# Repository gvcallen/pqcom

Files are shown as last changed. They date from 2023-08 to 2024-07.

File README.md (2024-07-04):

# PocketQube Satellite Communication System

## Overview
This repository holds code, datasheets, PCB schematics and other files related to the design and development of a PocketQube Satellite Communication System. This was done by Gary Allen in  partial fulfilment of the requirements of the module Project (E) 448 for the degree Baccalaureus in Engineering in the Department of Electrical and Electronic Engineering at the University of Stellenbosch, South Africa. PocketQubes are miniaturised satellites, and this project aimed to develop prototypes for the unit to be placed on the satellite, the ground station, and the PC interface. A video documenting the project can be found on YouTube at https://www.youtube.com/watch?v=bJcF6t-W-kM

## Code
This folder contains the relevant code for the project. Inside are 5 sub-folders. All embedded development was done using the *PlatformIO* extension on VS code, and all desktop GUI development was done using the *Qt* C++ library, both under WSL (Windows Subsystem for Linux). I highly recommend a linux install due to the ease of installation of the Qt libraries.
- ***gel*** is another Github repository created by myself containing the core embedded C++ classes used by the other projects. Even though it was developed solely for this project, I decided to make it an independent library so that it can be self-standing and potentially be used outside of the PocketQube project in the future.
- ***pqcu*** is the folder housing the code for the *PocketQube Communication Unit* i.e. the module to be placed on the PQ itself. It is very simple since it only "spits out" its GPS location via LoRa (i.e only downlink communication was implemented) however "gel" theoretically has an almost-ready foundation for dual-link communication (which was not implemented due to time constraints).
- ***pqgs*** contains code for the *PocketQube Ground Station*. This includes communication with the PQ unit, motor drive control, GPS tracking and serial control via a "TNC" (a.k.a a laptop connected via USB).
- ***pqui*** contains desktop GUI code to control the GS via USB and a PC. Theoretically, all control can be done via the terminal, however the GUI was implemented to make things slightly easier. It implements the SUNCQ protocol under ***Documents***.
- ***radiosonde_auto_rx*** was an extension of the project to receive data from a commercial Radiosonde via a software-defined radio (SDR). This is used by ***pqui***. Although the Radiosonde receiving is functional, it is currently implemented is a bit "messy", since a Python script is called and controlled from Qt, and this causes issues from time-to-time. If only "custom" communication is needed, this can be ignored.

## Other
The rest of the contents are relatively self-explanatory:
- ***datasheets*** contains various used (and not used) datasheets for ICs and modules.
- ***documents*** contains the SUNCQ protocol for PC to GS communication.
- ***images*** contains images taken throughout the project, such as during testing and final deployment.
- ***kicad*** contains the schematics developed for the PQ and the GS. The final Gerber files are also present in zip format. Note that some folders in here are old and need to be cleaned up.
- ***link-budget*** contains a pre-liminary link-budget done with free Python software.
- ***report*** contains the final report files for Latex. The final PDF is in the root of this folder.
- ***testing*** contains test results and data.

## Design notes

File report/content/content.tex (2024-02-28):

\titlespacing*{\chapter}{0pt}{0pt}{20pt}
\chapter{Introduction}
\subfile{introduction/overview}
\subfile{introduction/problem_statement}
\subfile{introduction/requirements}
\subfile{introduction/specifications}

\chapter{Background}
\subfile{background/pocketqube}
\subfile{background/satellite_tracking}
\subfile{background/antennas}
\subfile{background/telecommunication}
% \subfile{background/pcb_design}

\chapter{System Design}
% \subfile{system_design/overview}
\subfile{system_design/high_level_system}
\subfile{system_design/ground_station}
\subfile{system_design/pq_unit}

\chapter{Detailed Design}
\subfile{detailed_design/component_selection}
\subfile{detailed_design/ground_station_pcb}
\subfile{detailed_design/pq_unit_pcb}
\subfile{detailed_design/link_budget}
\subfile{detailed_design/ground_station_antenna}
\subfile{detailed_design/pq_unit_antenna}
\subfile{detailed_design/software}

\chapter{Implementation}
\subfile{implementation/ground_station_pcb}
\subfile{implementation/ground_station_antenna}
\subfile{implementation/pq_unit_pcb}
\subfile{implementation/pq_unit_antenna}
\subfile{implementation/software}

\chapter{Testing}
\subfile{testing/ground_station_pcb}
\subfile{testing/pq_unit_pcb}
\subfile{testing/radio_communication}
\subfile{testing/ground_station_antenna}
\subfile{testing/pq_unit_antenna}
\subfile{testing/gui}
\subfile{testing/range}
\subfile{testing/tracking}
\subfile{testing/radiosonde}
\subfile{testing/full_system}

\chapter{Conclusion}
\subfile{conclusion/summary}
\subfile{conclusion/future_work}

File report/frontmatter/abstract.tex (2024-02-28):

\chapter*{Abstract}
\addcontentsline{toc}{chapter}{Abstract}
\makeatletter\@mkboth{}{Abstract}\makeatother

This report documents the design and implementation of a wireless communication system for a miniaturised satellite called a \textit{PocketQube}. The PocketQube standard is a set of specifications which aim to make it easier for people to design small satellite modules that can easily integrate with each other. The standard is relatively new, however, and few designs have been published for a full PocketQube communication system that includes a ground station.

The design in this project includes both a tracking ground station, as well as a PocketQube module. The LoRa-based ground station was designed to mechanically track the satellite system using a pre-defined GPS path, as well as using satellite-received GPS data. The ground station was also designed to receive telemetry from existing radiosondes in the meteorological band. The system was then implemented, and the LoRa communication link was successfully tested up to 122 km line-of-sight at a baud rate of 9600 bps. This report documents the design choices made and constraints faced; discusses the methods uses during implementation; interprets the test results; and suggests improvements for future projects.

\selectlanguage{english}

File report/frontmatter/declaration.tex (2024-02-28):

%\chapter*{Declaration}
\newpage
\thispagestyle{plain}
\addcontentsline{toc}{chapter}{Declaration}
\makeatletter\@mkboth{}{Declaration}\makeatother

\centerline{}
\vspace*{-10pt}

\section*{\centering Plagiaatverklaring / \textit{Plagiarism Declaration}}

\vspace*{5pt}

\begin{enumerate}
    \item Plagiaat is die oorneem en gebruik van die idees, materiaal en ander intellektuele eiendom van ander persone asof dit jou eie werk is.\\
    \textit{Plagiarism is the use of ideas, material and other intellectual property of another's work
        and to present it as my own.}
    
    \item Ek erken dat die pleeg van plagiaat 'n strafbare oortreding is aangesien dit 'n vorm van diefstal is.\\
    \textit{I agree that plagiarism is a punishable offence because it constitutes theft.}
    
    \item Ek verstaan ook dat direkte vertalings plagiaat is. \\
    \textit{I also understand that direct translations are plagiarism.}
    
    \item Dienooreenkomstig is alle aanhalings en bydraes vanuit enige bron (ingesluit die internet) volledig verwys (erken). Ek erken dat die woordelikse aanhaal van teks sonder aanhalingstekens (selfs al word die bron volledig erken) plagiaat is. \\
    \textit{Accordingly all quotations and contributions from any source whatsoever (including the internet) have been cited fully. I understand that the reproduction of text without quotation marks (even when the source is cited) is plagiarism}
    
    \item Ek verklaar dat die werk in hierdie skryfstuk vervat, behalwe waar anders aangedui, my eie oorspronklike werk is en dat ek dit nie vantevore in die geheel of gedeeltelik ingehandig het vir bepunting in hierdie module/werkstuk of 'n ander module/werkstuk~nie. \\
    \textit{I declare that the work contained in this assignment, except where otherwise stated, is my original work and that I have not previously (in its entirety or in part) submitted it for grading in this module/assignment or another module/assignment.}
\end{enumerate}

\vfill

\noindent \begin{tabularx}{1.0\linewidth}{|L|L|}
    \hline
    \vspace{1cm} {Studentenommer / \textit{Student number}} & \vspace{1cm} {Handtekening / \textit{Signature}} \\
    \hline
    \vspace{1cm} {Voorletters en van / \textit{Initials and surname}} & \vspace{1cm} {Datum / \textit{Date}} \\
    \hline
\end{tabularx}

\vspace{15pt}

% The old declaration

%I, the undersigned, hereby declare that the work contained in this report is my own original work unless otherwise stated.
%
%% Afrikaans:
%% Hiermee verklaar ek, die ondergetekende, dat die werk in hierdie verslag vervat my eie oorspronklike werk is, tensy anders vermeld.
%
%\vspace{2.5cm}
%
%\begin{table}[h]
%\begin{tabular}{@{}p{2.5cm}p{5cm}}
%    Signature: & \dotfill \\
%    & \multicolumn{1}{c}{Obi-Wan Kenobi} \\
%    ~\vspace{1cm} \\
%    Date: & \dotfill \\
%\end{tabular}
%\end{table}
%
%\vfill
%
%\begin{center}
%    Copyright \textcopyright\ 2099 Stellenbosch University \\
%    All rights reserved
%\end{center}

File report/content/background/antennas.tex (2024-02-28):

\graphicspath{{./figures}}

\section{Antennas}\label{sec:antenna_theory}

This section covers a very brief review of different types of antennas in literature, as well as how to practically feed these antennas with a transmission line, and a summary of their varying performances.

\subsection{Types}\label{sec:antenna_types}
There are various antenna types to consider for a satellite communication system. A highly customized design is out of the scope of this project, and therefore only designs with tunable parameters, or existing designs in literature, will be considered. Ultimately, each antenna's \textit{radiation pattern}, \textit{gain} (dBi i.e. decibels relative to an \textit{isotropic} source), fractional \textit{bandwidth}, main lobe \textit{beamwidth}, dimensions, and polarization will be compared. Here, \textit{polarization} refers to the orientation of the EM wave i.e. horizontal, vertical or circular.

\subsubsection{Half-Wavelength Dipole}

\begin{figure}[!htb]
  \begin{minipage}{.55\textwidth}
    \centering
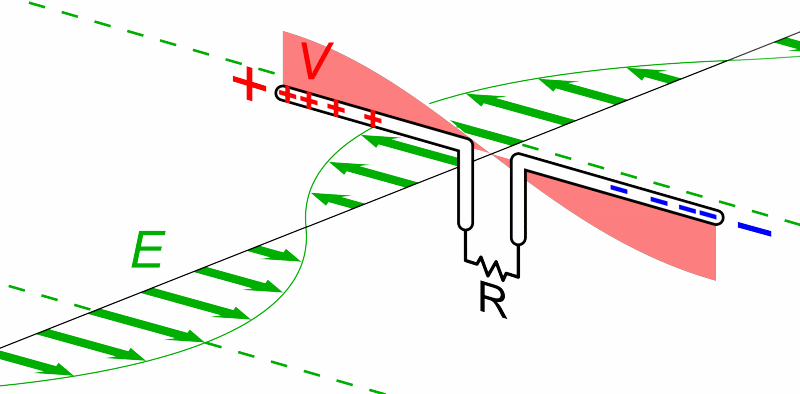
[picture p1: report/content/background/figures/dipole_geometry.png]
    
    \caption{Dipole Antenna Geometry \cite{site-dipoleAntenna}}
    \label{fig:dipole_geometry}
  \end{minipage}
  \begin{minipage}{.44\textwidth}
    \centering
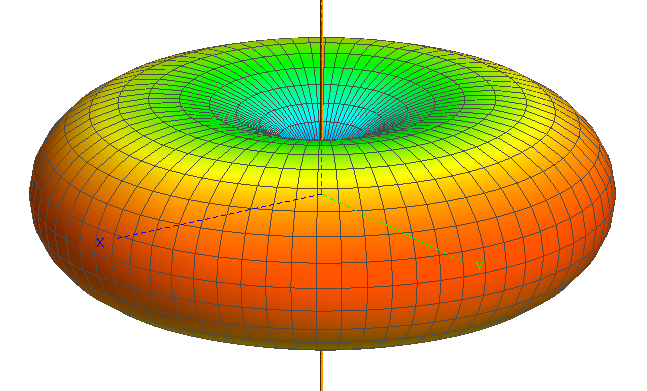
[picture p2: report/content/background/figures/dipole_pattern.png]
    
    \caption{Dipole Antenna Radiation Pattern}
    \label{fig:dipole_pattern}
  \end{minipage}
\end{figure}

The half-wavelength ($0.5 \lambda$) dipole anntenna is arguably the simplest and most common type of antenna. It consists of two conductive elements operating in opposite phase, as depicted in Figure \ref{fig:dipole_geometry}. It is described as having a donut-shaped radiation pattern as in Figure \ref{fig:dipole_pattern}, with \textit{omni-directional} radiation in the plane perpendicular to the conductor, and a \textit{null} tangential to the conductor. It has a maximum gain of 2.15 dBi, and is linearly polarized. \cite{site-antennaTheory}

\subsubsection{Quarter-Wave Monopole}\label{monopole}
The working principle of a monopole antenna makes use of the electromagnetic theory of \textit{imaging}. If an infinite ground plane or Perfect Electrical Conductor (PEC) is placed below one half of a $0.5 \lambda$ dipole antenna, since the PEC holds the constraint that the tangential electric field is zero across its boundary, an equal but opposite electromagnetic wave is ``induced" due to the incident wave. This wave ``appears" to have come from an equal but oppositely polarized ``image" source, hence removing the need for the second half of the dipole to be present.

These antennas are extremely useful when size is a constraint, however have the disadvantage of requiring a ground plane. A \textit{whip} antenna is a form of monopole antenna designed to be flexible so that it does not break as easily. It often is used without a ground plane, which results in reduced performance, shown in Figure \ref{fig:whip}. \cite{site-antennaTheory}

\begin{figure}[!htb]
  \begin{minipage}{.49\textwidth}
    \centering
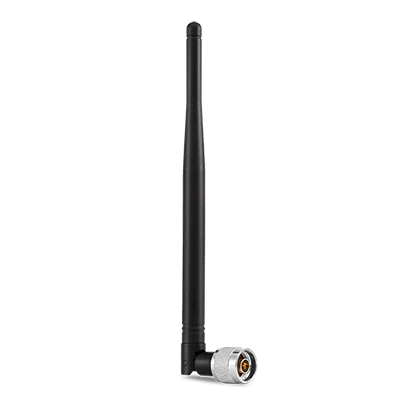
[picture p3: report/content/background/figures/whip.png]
    
    \caption{A Monopole Whip Antenna in a Plastic Housing \cite{site-whipAntenna}}
    \label{fig:whip}
  \end{minipage}
  \begin{minipage}{.49\textwidth}
    \centering
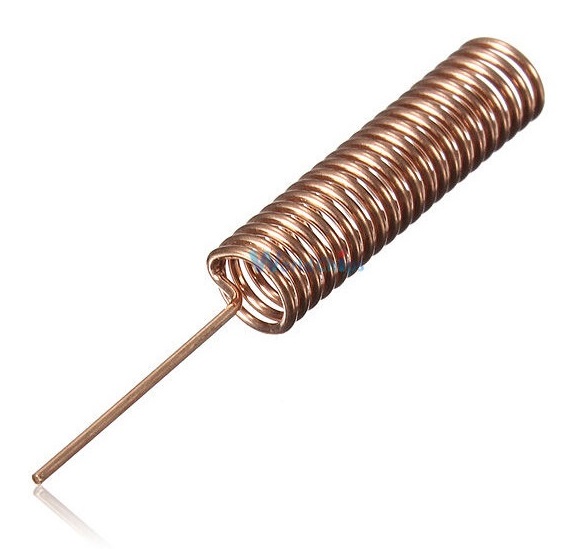
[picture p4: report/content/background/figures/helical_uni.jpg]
    
    \caption{A 21-turn Copper Helical Antenna \cite{site-helicalAntenna}}
    \label{fig:helical_uni}
  \end{minipage}
\end{figure}

\subsubsection{Helical}
Helical antennas are coiled windings of wire, where the circumference of the coil has some relationship with the desired frequency. Commonly, a circumference of $C = 1.0 \lambda$ is used for \textit{uni-directional} or \textit{axial mode} variants. In this case, a ground plane is required. The ground plane can also be \textit{cupped} (i.e. extended as an open cylinder) for additional directivity \cite{textbook-antennaTheoryAnalysisDesign}. \textit{Omni-directional} or \textit{normal mode} variants are possible without a ground plane, when $C << \lambda$. Figure \ref{fig:helical_uni} depicts a 21-turn example of such an antenna.

Helical antennas have several design parameters that influence the antenna's characteristics, such as number of turns ($n$), wire width ($wd$), and spacing between turns ($S$). A spacing of $0.20 \lambda < S < 0.25 \lambda$ is recommended, however smaller spacings of $0.10 \lambda < S < 0.20$ are commonly used \cite{site-helicalCalculator}. These antennas are also capable of either linear or circularly polarized signals. Lastly, since they can be designed with an arbitrary number of turns, and they have a large operating bandwidth, they can be made smaller than other alternatives.

\subsubsection{Patch}
A \textit{patch} or \textit{PCB} antenna is simply a rectangular PCB trace sized correctly to allow for radiation. Typically, a simple square or rectangular shape can be used. They allow for small profiles at the cost of efficiency \cite{site-antennaTheory}, and have either circular or linear polarization.

\subsubsection{Array}
In general, multiple antennas can be combined in an \textit{array} configuration. This allows complete manipulation of the design (such as the desired gain), by virtue of \textit{constructive} and \textit{destructive} interference of the electromagnetic waves. Common variations of this concept reside in \textit{Yagi-Uda} and \textit{Patch Array} antennas. \cite{site-antennaTheory}

\subsubsection{Yagi-Uda}
\begin{figure}[!htb]
  \begin{minipage}{.49\textwidth}
    \centering
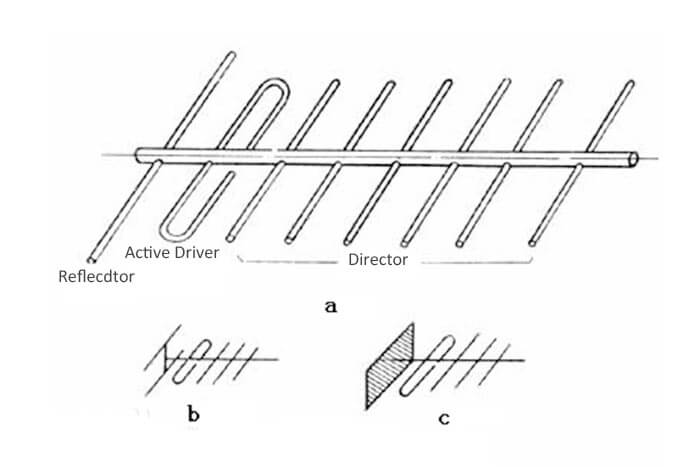
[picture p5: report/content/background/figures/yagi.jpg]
    
    \caption{Yagi-Uda Antenna Geometry \cite{site-icantennasYagi}}
    \label{fig:yagi}
  \end{minipage}
  \begin{minipage}{.49\textwidth}
    \centering
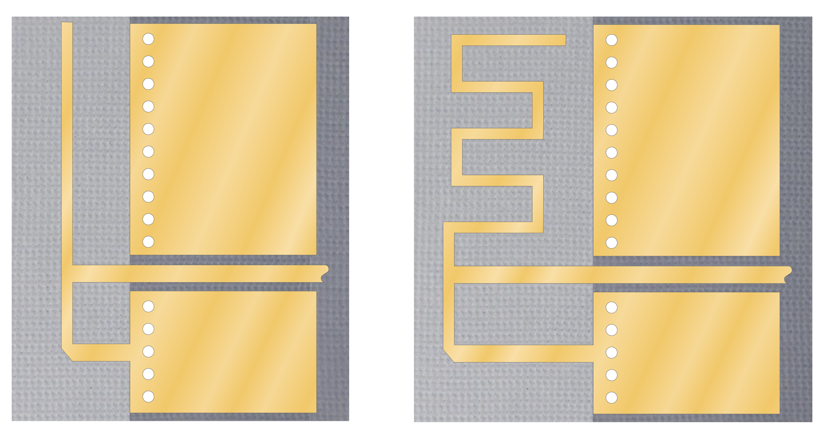
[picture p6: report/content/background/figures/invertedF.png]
    
    \caption{Two Inverted-F Microstrip Antenna Geometries \cite{site-invertedFAntenna}}
    \label{fig:invertedF}
  \end{minipage}
\end{figure}

Although not strictly an antenna array, \textit{Yagi-Uda} antennas are one of the most popular directive antennas that make use of interference. A given number of passive conductors are stacked in a specific configuration as show in Figure \ref{fig:yagi}, ultimately steering the EM waves using the concept of interference. Only one of the conductors in the array is fed with the signal. They generally can be made to have very large gain, and are linearly polarized. A \textit{cross-Yagi} is a variation on this design which allows for circular polarization.

\subsubsection{Microstrip}
\textit{Microstrip} antennas generally refer to any planar, PCB antenna. They can be considered a generalization of a patch antenna. Many variations exist due to their flexible nature. A few examples include: a \textit{patch array}; an \textit{inverted-F} design, which has a small form factor and a nearly 3D omni-directional radiation pattern; a \textit{ring antenna} \cite{paper-lowProfileRingAntenna}, which is uni-directional, and has an even smaller form factor than the inverted-F antenna; and a \textit{helical patch} antenna, which is simply a ``zig-zag" helix shape flattened onto a PCB.

\subsection{Feedlines}
In general, \textit{feeding} an antenna is more complicated than simply connecting the amplifier's positive and negative terminals to the antenna's terminals. A $\SI{50}{\ohm}$ characteristic impedance is often used in RF systems. Since each antenna has a unique \textit{input impedance} which is generally different from this value, it must be \textit{matched} appropriately for optimal performance. A few well-known techniques for a number of the antennas in Section \ref{sec:antenna_types} are reviewed below.

\subsubsection{General}
A general, antenna-agnostic narrow-band technique for antenna impedance matching is to employ a ``lumped element" matching circuit consisting mainly of inductors and capacitors. The most common example of this is an L-section, with exactly one capacitor and inductor.

\subsubsection{Half-Wavelength Dipole}
A half-wavelength dipole antenna has an input impedance of around $\SI{73}{\ohm}$, varying only due to the wire diameter used. A common method to reduce this impedance to $\SI{50}{\ohm}$ is simply to reduce the length of the dipole. In this case, a $\SI{50}{\ohm}$ match occurs from $0.42\lambda$ to $0.44\lambda$. \cite{textbook-antennaTheoryAnalysisDesign}

\subsubsection{Helical}\label{sec:helical_matching}
The input impedance of a helical antenna varies between 100 and 200 ohms. A common method to reduce this impedance is for the first quarter turn of the helix to be in the form of a conductive strip, and for the \textit{pitch angle} of this section to be close to zero \cite{textbook-antennaTheoryAnalysisDesign}. The height above the ground plane can then be varied to match the antenna appropriately, with the following equation approximately providing a $\SI{50}{\ohm}$ match \cite{textbook-antennaTheoryAnalysisDesign}:
$$h = \frac{w}{\frac{377}{\sqrt{\epsilon_r} Z_0} - 2}$$

\subsection{Summary}
It is useful to have a qualitative comparison of different antenna types as a reference for the design phase. This is presented in Table \ref{tab:antenna_characteristics} in the appendix, and has been tabulated using both the previous research, and general consensus in literature. Note that a \textit{narrow} beamwidth generally corresponds to a \textit{uni-directional} antenna (and wide for omni-directional) and therefore this characteristic has not been included in the table.

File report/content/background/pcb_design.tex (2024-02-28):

\graphicspath{{./figures}}

\section{PCB Design}

\textit{Printed circuit board} (PCB) design is considered a skill and art in and of itself. Since this project will require basic PCB design techniques related to simple circuits, as well as potentially RF circuits (depending on decisions made in the design process), an initial review of literature and techniques should be done. A very brief overview of the most relevant, core concepts is presented.

\subsection{Layers}
\begin{figure}[!htb]
  \centering
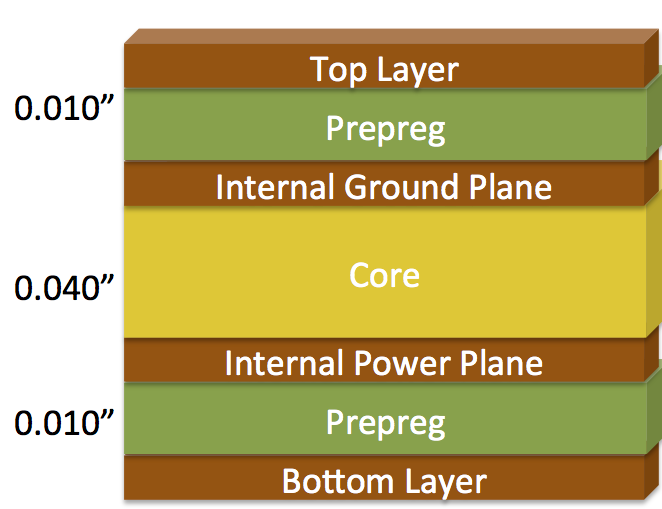
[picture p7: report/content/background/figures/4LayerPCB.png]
  
  \caption{Common 4 Layer PCB Stackup \cite{site-4layerPCB}}
  \label{fig:4layerPCB}
\end{figure}

A PCB is made up of multiple layers. 2-layer and 4-layer PCBs are considered the most common. For a 2-layer board, there are two layers of copper on both the top and bottom of the board. For 4-layer boards, 2 extra copper layers lie in between the outer layers and are therefore not exposed to air. These inner layers are general used for \textit{ground planes} or \textit{power planes}. The purpose of each layer and how they are distributed is called the PCB \textit{stackup}. Figure \ref{fig:4layerPCB} shows a common 4-layer PCB stackup. \cite{site-pcbLayers}

\subsection{Traces}
The traces connect various components on the different layers. They are created by removing the copper which surround them, resulting in a single conducting path. For digital design, generally only the thickness of the trace is important, and is determine by the current handling requirements of that signal. For radio frequency \textit{RF} design, the type of material in between traces, distance between traces, thickness of the trace etc. should all be taken into account. This is due to the fact that they influence the \textit{characteristic impedance} of the resulting \textit{transmission lines}.

\subsection{Vias}
Vias are holes on boards that (generally) pass a signal from one layer to another. They allow for a circuit's components to be distributed across layers, therefore providing flexibile in laying traces. \textit{Untented} (uncovered) vias can be soldered to for e.g. \textit{through-hole} components, whereas \textit{tented} vias are used to prevent the via from being soldered to \cite{site-pcbBasics}. \textit{Stiching vias} are a large number of vias placed in a spaced-out pattern, which result in a stronger connection, allow for better thermal management, and reduce crosstalk and EMI \cite{site-viaStitching}.

\subsection{Copper Pours}
\textit{Copper pours} are large areas of copper on a PCB. They are typically used for large exposed ground planes and power planes where power distribution or electrical shielding is necessary.

\subsection{RF Design}\label{sec:pcbRFDesign}
The design of PCB circuits involving higher frequencies is significantly more complex. Not only is the layout of components more critical, but the length of traces, the placement of ground planes, and many complex considerations need to be made. Some of this process can be significantly simplified by making use of RF \textit{modules}. These are typically isolated components with an RF \textit{shield} providing a single functionality.

The following list encompasses a short summary of some considerations that \textit{may} be applicable in this project. It should be noted that many of these points are \textit{only} applicable if RF traces and RF ICs are designed directly (as opposed to using an RF module). This is known as a ``chip-down" design. The trade-off of using such modules will be made in the design phase.
\begin{itemize}
    \item Ensure proper grounding with thick enough traces and $V_{cc}$ bypas capacitors near RF integrated circuits. If the ground is not on the same layer as the IC, multiple vias should be used \cite{datasheet-MAX2659}. 
    \item If a high-frequency signal is to be routed on a trace longer than the frequency's critical length (taken to be $\frac{\lambda}{10}$ \cite{site-pcbRoutingGuidelines}), its characteristic impedance should either be \textit{controlled} or \textit{matched} appropriately. In other words, if two $\SI{50}{\ohm}$ RF pins on two different ICs are to be connected together, either the trace itself should have a $\SI{50}{\ohm}$ impedance, or impedance matching should be done so that the transition between characteristic impedances does not cause reflections. \cite{datasheet-MAX2659}
    \item Take care of \textit{crosstalk} and electromagnetic \textit{isolation}. Use \textit{RF filters}, \textit{RF shields} and \textit{stitching vias} to minimize these effects.
    \item Keep RF lines as far as possible from each other, and route high-speed digital signals on a different layer from the RF lines entirely. Layers should be dedicated to a continuous ground plane and power plane - typically layers 2 and 3 for a 4-layer board, as shown in Figure \ref{fig:4layerPCB}. \cite{site-rfPCBGuidelines}
    \item Apply curved bending or \textit{mitering} when transmission lines are required to change direction abruptly. \cite{site-rfPCBGuidelines}
\end{itemize}

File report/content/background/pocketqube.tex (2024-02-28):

\graphicspath{{./figures}}

\section{PocketQube}

The PocketQube standard is a fairly new set of protocols and specifications defining a modularized nano-satellite system. The term \textit{modularized} in this context refers to the ability for different ``modules" or PocketQube units, each with their own set functionality, to be connected to a common \textit{backplane} (as in Figure \ref{fig:pq_backplane}) and integrated seamlessly. \textit{Integration} here refers to both the mechanical spacing of each module, as well as the electronic communication between the modules.

As an example, a PocketQube enclosure could contain three units: a communication module, a sensor pack, and a battery system. These modules can then be connected onto a PCB backplane via headers, placed inside a single enclosure (such as that in Figure \ref{fig:pq_enclosure}) and either launched into orbit, or released as a balloon satellite payload.

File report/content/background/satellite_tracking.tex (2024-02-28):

\graphicspath{{./figures/}}

\begin{figure}[!htb]
  \begin{minipage}{.49\textwidth}
    \centering
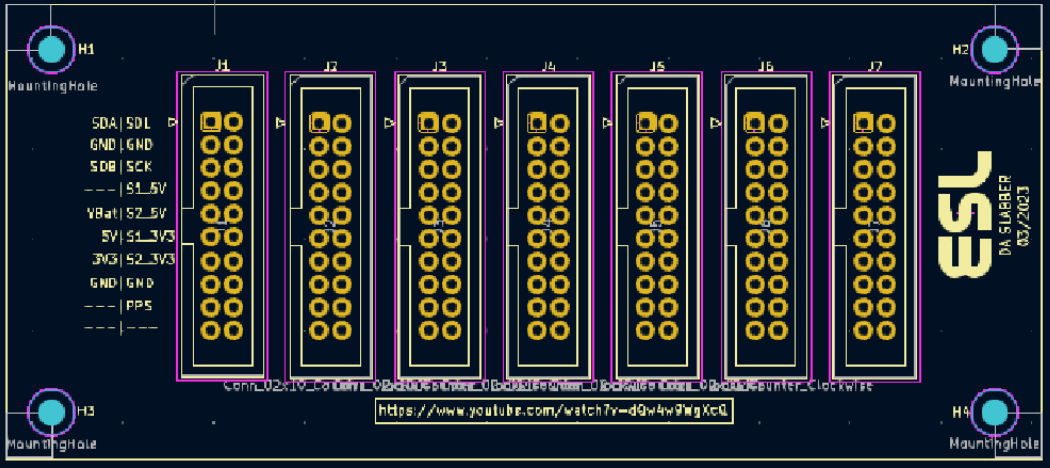
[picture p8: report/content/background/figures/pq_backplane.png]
    
    \caption{A Stellenbosch PocketQube Backplane PCB \cite{standard-pqsu}}
    \label{fig:pq_backplane}
  \end{minipage}
  \begin{minipage}{.49\textwidth}
    \centering
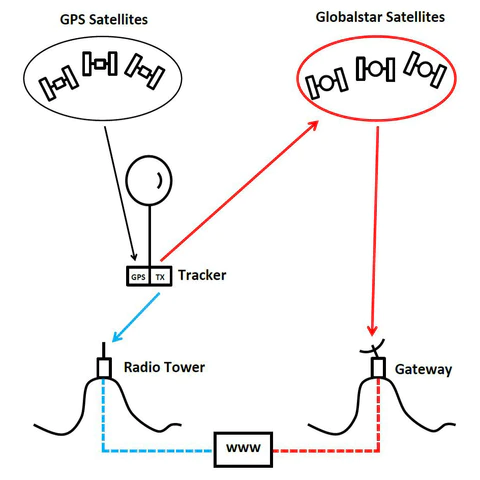
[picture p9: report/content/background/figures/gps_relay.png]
    
    \caption{GPS Relay Tracking \cite{site-highaltitudescienceTrackingWeather}}
    \label{fig:gps_relay}
  \end{minipage}
\end{figure}

\section{Satellite Tracking}

\subsection{Open-Loop}
Arguably the simplest tracking method is commonly referred to as ``open-loop" tracking. Here, only information about the predicted flight path of the balloon/satellite is used, such as expected GPS co-ordinates at different points in time.

Given geographical co-ordinates of both the ground station and the satellite (with e.g. a \textit{WGS84} datum), \textit{Mercator projection} can be used to obtained a cartesian pointing vector \cite{site-mercator}. The ground station can then simply be pointed in that direction at each instant in time. The flight path can either be a pre-calculated path (as demonstrated in Figure \ref{fig:balloon_path}), or can be continuously re-estimated based on real-time weather data. \textit{Habhub} is an online high-altitude path predictor \cite{site-habHub} which is freely available for this purpose.

An advantage of this method lies in its extreme simplicity to implement. It has several disadvantages, however, including being vulnerable to prediction inaccuracies, as well as the difficulty experienced in re-acquiring the communication link once it is lost. Further, a GPS receiver is generally still required on the ground station, unless it is positioned with a pre-determined location and orientation, or an external GPS.

\subsection{GPS (Direct)}
If an initial communication link can be established between the satellite and ground station, \textit{direct} GPS transmission can be added for positional feedback. This is a simple method of ``closing" the tracking loop, since the path data can be updated dynamically. Generally, both the PQ and GS GPS co-ordinates are required as input to the system.

\subsection{GPS (Relay)}
If a link cannot be initially established, a ``relay" method of GPS tracking can be used. This method functions in a three-step process, explained below and depicted in Figure \ref{fig:gps_relay}:
\begin{enumerate}
    \item The precise position of the payload and the ground station is determined using data received from GPS satellites.
    \item The position is \textit{relayed} to an external network (satellite or ground -based) using a radio transmitter.
    \item The ground station receives the location from the external network (e.g. via the internet).
\end{enumerate}

The major disadvantage of this method is the additional cost required. Since an antenna capable of communicating with one of the external networks is required, two antennas are needed if direct communication with a ground station is desired (however this is usually no longer necessary as the relay network can be used). Further, the cost of subscribing to an external network is generally high.

This type of tracking works well if the satellite is physically close to the external network satellites, or if the ground station does not need to communicate in real-time (but only needs access to the location of the satellite e.g. in a home-made balloon satellite launch).

\subsection{Signal Strength}
Radio tracking can be done when the satellite itself transmits omni-directionally. The received signal strength can be used as feedback to determine the direction to point. To initially find the satellite, the entire sky can be scanned using a ``brute force" procedure, or an initial guess can be provided. Then, periodic \textit{radius scanning} can be used to track the signal within a certain portion of the sky. More advanced techniques are also available, such as \textit{conical scanning}, which allows direction calculation of a new pointing direction given a set of conical signal strength measurements.

This method provides great flexibility, since no satellite path information is required, however it is generally not necessary when a reasonable initial guess is available, and an antenna with a reasonably large beamwidth is used.

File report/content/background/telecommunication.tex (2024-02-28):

\section{Telecommunication}\label{sec:telecommunication_theory}

\subsection{Modulation Techniques}
The \textit{modulation} technique used over a digital communication link refers to the method used to represent bits as electrical signals. Common techniques are compared below.

\begin{table}[!htb]
  \centering
  \renewcommand{\arraystretch}{1.2}
  \hspace*{-0.5cm}
  \begin{tabular}{ |p{3cm}|p{2cm}|p{11cm}| }
  \hline
  \textbf{Name}                & \textbf{Bit Variation}    & \textbf{Comments} \\ \hline
   Amplitude Shift Keying (ASK)
   & Amplitudes
   & Poor noise immunity
   \\ \hline
   Frequency Shift Keying (FSK)
   & Frequencies
   & Simple to implement. Can be filtered for decreased bandwidth, and is then known as \textit{Gaussian-FSK} (GFSK).
   \\ \hline
   Phase Shift \mbox{Keying} (PSK)
   & Phase \mbox{Angles}
   & Similar to FSK or QAM. Lower spectral efficiency than QAM.
   \\ \hline
   Quadrature Amplitude Modulation (QAM)
   & Amplitude-Phase Pairs
   & Very high spectral efficiency. Commonly used in higher cost, high throughput systems.
   \\ \hline
   LoRa (``Long-Range") Modulation
   & Frequency-varying ``Chirps"
   & Can drastically increase range, at the expense of greater bandwidth requirements \cite{datasheet-SX1278}. Practically demonstrated in an existing CubeSat system \cite{design-FOSSASATLink}.
   \\ \hline
  \end{tabular}
  \caption{Comparison of Modulation Techniques}
  \label{tab:modulationTechniques}
\end{table}
\vspace*{-\baselineskip}

\subsection{Link Budget}\label{sec:link_budget}
For any communication system, a \textit{link budget} should be estimated, with the goal of taking into account transmitter power, antenna characteristics, receiver sensitivity, and any attenuation involved. A number of the attenuation affects include: cable loss; amplifier-antenna mismatch; free-space path losses; absorption losses due to clouds and rain; \textit{polarization} mismatch due to antennas not being aligned; \textit{scintillation} effects due to changes in the air's refractive index; and the effect of varying \textit{elevation angles} \cite{design-satelliteLinkBudget}. It is recommended to include a minimum \textit{fade margin} of at least 3 dB for low frequency links \cite{paper-linkMargin}; 10 dB for links that require more up-time \cite{design-linkBudgetDesign}; and 20 dB for critical links.

\subsection{Protocols}
A few link-layer and network-layer protocols already exist that facilitate nano-satellite applications. 
The CubeSat Space Protocol (CSP) \cite{standard-csp} is a fully-fledged network layer protocol for CubeSat embedded systems. It allows for all devices in the satellite ecosystem (satellite modules, the ground station, a control computer etc.) to communicate ``directly" with each other via \textit{packet forwarding}. It relies on various link and network -layer protocols, including KISS, I2C and CCSDS (\textit{Consultative Committee for Space Data Systems}).

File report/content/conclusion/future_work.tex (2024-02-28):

\section{Future Work}\label{sec:future_work}

There are various improvements and alternative choices that could be explored in the context of the developed system:
\begin{itemize}
    \item \textit{Improved ground station PCB}. The ground station PCB was designed to use break-out boards, through-hole components, and modules for rapid development. Future designs could replace almost all components with surface-mounted ones, and remove break-out boards (e.g. the ESP32 board) to reduce cost, improve connection integrity, and allow more space for additional components.
    \item \textit{Improved helical antenna construction}. The ground station antenna can be optimised, by constructing it using more rigid materials to stricter manufacturing tolerances. This would hopefully decrease any variance between the simulation and the implementation, and improve the matching and radiation pattern. A longer antenna with higher gain could also potentially be implemented if similar materials are used, considering that the mass-distance product of the implemented antenna was under half of the theoretical maximum.
    \item \textit{Automatic orientation detection}. Currently, the ground station uses a dead-reckoning fix, requiring that it be pointed towards magnetic north, and that it is orientated flat. Further work could be done to make use of an IMU in order to allow the ground station to be rotated at any angle, with its orientation being automatically compensated for in software.
    \item \textit{PocketQube antenna integration}. The antenna for the PocketQube was not designed to be deployable, but the half-dipole was shown to provide an effective proof-of-concept. For integration into final PocketQube models, options include a deployable antenna (e.g. with a foldable spring mechanism); using a higher frequency band; or using a much smaller but lower efficiency normal-mode helical antenna.
    \item \textit{Radiosonde link optimisation}. A dedicated, more sensitive radiosonde receiver targeted at the meteorological band (as opposed to a generic software-defined radio) could be implemented. This might require an RF switch, but would provide the ability to change between the custom and radiosonde link in software.
    \item \textit{Signal strength scanning}. Faster signal strength ``conical" scanning could be explored. Although it was not investigated in this project (as a brute-force scan or open-loop estimate is generally sufficient to initially find the payload and receive its GPS location), the flexibility of tracking the payload using only its received radio signal may be beneficial.
    \item \textit{PocketQube assembly}. Since a prototype for all the sub-systems of a PocketQube communication system have been designed and tested, integration within an actual PocketQube housing can be investigated, and an actual PocketQube satellite can become a reality.
\end{itemize}

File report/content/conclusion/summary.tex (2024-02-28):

\section{Summary}

A PocketQube communication system, with a tracking ground station and a PocketQube PCB module, was successfully designed to meet the system requirements for a balloon satellite launch in Saldanha Bay. Unfortunately, the launch did not take place, however several modularized tests helped to prove that the system is fully functional and capable of communicating over the required distances.

LoRa proved to be a viable choice for the custom communication link. Not only did the link meet the throughput requirements of 9600 baud, but the system's range was successfully tested up to 122 km line-of-sight. Further, the increased immunity due to the spread-spectrum technology suggests that it should be made a priority choice for low-cost, low-power satellite communication links. The helical antenna design also proved to be effective in the context of the project, as it was easy to manufacture, and allowed the system to meet its requirements.

The open-loop tracking method was successfully implemented, however was not integrated into a full-system test. Closed-loop GPS tracking was successfully tested for a weather balloon launch up to a range of 25 km, and appeared to be the preferred tracking method for balloon satellite systems, since an initial GPS fix was easy to establish.

Lastly, the final ground station and PocketQube module PCB designs and implementations were shown to be effective, allowing a good foundation for future work.

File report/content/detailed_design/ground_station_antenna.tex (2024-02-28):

\graphicspath{{./figures}}

\section{Ground Station Antenna}
\subsection{Mechanical Considerations}

The existing antennna mount is shown in Figure \ref{fig:antennaMount}. Azimuthal and elevation stepper motors are connected directly through Gear A and B respectively. Gear A rotates the centre shaft to provide azimuthal steering, whereas Gear B rotates through Gear D and Gear E to allow a change in elevation. The 
specifications in Table \ref{tab:mount_specifications} were realized.

The black plastic platform is triangular and has three mounting holes. The new ground station's antenna should therefore be mounted onto this platform. It is important to consider the forces/torques involved, as well as the stepper motor holding torques, in order to determine the maximum weight and acceptable form factor of the new antenna.

The azimuthal motor need not be considered, as all torques from the mount to its base are perpendicular to the central shaft, meaning it would only need to overcome static frictional forces to rotate the antenna, which are assumed to be negligible. The holding torque of the elevation motor, however, will constrain the antenna design. The holding torque of each motor is 0.25 Nm. The gearing ratio resulting from Gears B, D and E, results in an approximate 8x torque increase. This provides a holding torque of around 2 Nm at the pivot axle.

The centre of gravity of the antenna, as well as its weight, will affect the motor's ability to hold it in place. The horizontal distance between the pivot axle and the mount in the upright position is measured to be 40mm. Therefore, in the worst-case (when the mount is upright as in Figure \ref{fig:antennaMount}), a planar antenna could weigh up to $\frac{2}{(9.8 \times 0.04)} = \SI{5.1}{kg}$. In general, the ``mass-distance" product of the antenna (mass times distance of centre of gravity from mount) should not be more than $\SI{0.2}{kg \cdot m}$. This should be strongly considered if a longer antenna is desired.

The physical dimensions of the antenna's ground plane is also constrained. A circular ground plane may make contact with the mount's base at low elevation angles (assuming the ground station itself is raised above the ground). When the mount is resting, this constraint is imposed when the ground plane first makes contact with the mount's base. For a circular ground plane, this is around $\SI{360}{mm}$ diameter at an elevation angle of around 35 degrees.

\subsection{Theoretical Design}
As discussed, the antenna should be capable of receiving from both radiosondes (around 405 MHz), as well as the custom LoRa-based link in the amateur radio band of 430 to 440 MHz. A helical antenna is suggested, for the following reasons:
\begin{itemize}
    \item Ability to increase gain arbitrarily by increasing the number of windings
    \item High fractional bandwidth of 50\% to 60\%, which may allow for a smaller antenna
    \item Ease of manufacture
\end{itemize}

The centre frequency $f_c$ of the antenna should first be selected. With a fractional bandwidth of 56\%, the inequality $f_c \times (1 - \frac{0.56}{2}) < \SI{405}{MHz}$ must hold. This gives an upper bound on the centre frequency of 562.5 MHz. A minimum ground plane diameter of no smaller than $0.5 \lambda$ is recommended in \cite{textbook-antennaTheoryAnalysisDesign}, and $0.75 \lambda$ in \cite{textbook-helicalAntenna}. It is, however, probable that a ground plane as small as $0.5 \lambda$ will adversely affect the radiation pattern near the end of the specified bandwidth.

Assuming the larger ground plane recommendation, the resulting ground plane diameter is $0.75 \times \frac{3e8}{562.5e6} = \SI{400}{mm}$, which is larger than the mechanical size constraint. Neverthless, $f_c = \SI{550}{MHz}$ is chosen as the initial centre frequency for simulations. The ground plane will then be decreased in size appropriately (towards $G_\lambda = 0.5$ i.e. \SI{270}{mm}) and the results observed.

The design parameters for a helical antenna are $f_c$ (centre frequency), $n$ (number of turns), $S$ (the spacing between turns), $C$ (the circumference) and $G$ (the ground plane diameter). Design formulae are provided in \cite{textbook-antennaTheoryAnalysisDesign}, and have been modified below to use relative values instead of absolute ones (i.e. $S_\lambda$ and $C_\lambda$ instead of $S$ and $C$). Directivity, in dBi, is given by:
$$
D_0 = 10 \log(15 \cdot n S_\lambda \cdot C_\lambda)
$$

$C_\lambda$ is typically kept at 1.0, meaning the cirumference is equal to the operating wavelength. As mentioned, a gain of around 5 dBi is required. However, a 3 dB bandwidth drop is estimated nearer to 400 MHz since it is the edge of the operating band. Further, the effect of a smaller ground plane will likely decrease performance by an estimated minimum of at least 1 dB. Therefore, a centre-frequency gain greater than 8 dBi will be designed for. This will also move the system towards the 20 dBi link margin. For this gain, the $n S_\lambda$ product should equal around 0.45. Although the optimal value for $S_\lambda$ is 0.23 \cite{textbook-antennaTheoryAnalysisDesign}, smaller values have been quoted to work \cite{site-helicalCalculator} and are mechanically easier to construct. Therefore, $S_\lambda = 0.15$ is chosen, and finally, $n \geq 3$.

\subsection{Simulation Design}
Simulation of a helical antenna is well documented in literature, and therefore the parameters can be varied iteratively and integrated into the antenna design process. For this project, FEKO software is used.

An initial model with the above parameters and a wire diameter of $\SI{2.5}{mm}$ (chosen due to availability) is simulated at the lower frequency of $f = \SI{405}{MHz}$. This is done for ground plane sizes $G_\lambda = 0.5$ and $G_\lambda = 0.7$ ($G = \SI{273}{mm}$ and $G = \SI{382}{mm}$). Most of the follow-up design is conducted around this frequency.

The resultant radiation patterns are shown in Figures \ref{fig:helix3_pattern_405MHz} and \ref{fig:helix2_pattern_405MHz} respectively. It is clear that the recommended value of $G_\lambda = 0.5$ from \cite{textbook-antennaTheoryAnalysisDesign} will not work near this lower frequency, as shown by the morphed radiation pattern. The pattern is found to be acceptable at around $G_\lambda = 0.7$.

\begin{figure}[!htb]
  \begin{minipage}{.48\textwidth}
    \centering
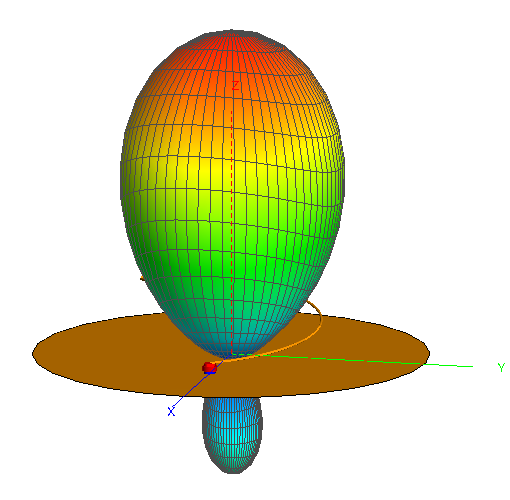
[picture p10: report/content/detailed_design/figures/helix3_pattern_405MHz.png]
    
    \caption{Simulated Helical \mbox{Antenna} Pattern at $f = \SI{405}{MHz}$ ($f_c = \SI{550}{MHz}$, $G_\lambda = 0.7$)}
    \label{fig:helix3_pattern_405MHz}
  \end{minipage}
  \begin{minipage}{.48\textwidth}
    \centering
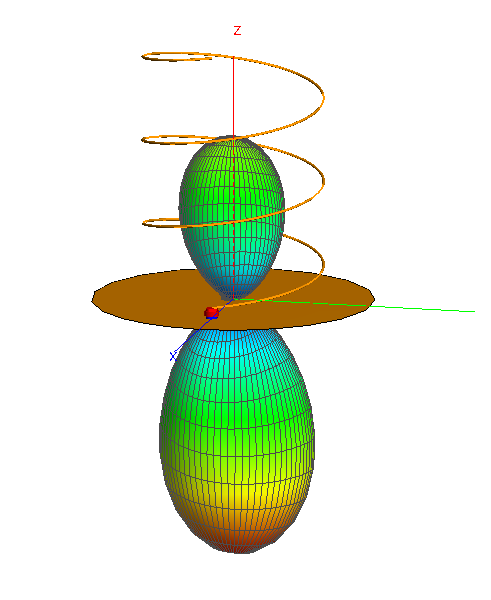
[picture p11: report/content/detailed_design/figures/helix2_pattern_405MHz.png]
    
    \caption{Simulated Helical \mbox{Antenna} Pattern at $f = \SI{405}{MHz}$ ($f_c = \SI{550}{MHz}$, $G_\lambda = 0.5$)}
    \label{fig:helix2_pattern_405MHz}
  \end{minipage}
\end{figure}

\begin{figure}[!htb]
  \begin{minipage}{.49\textwidth}
    \centering
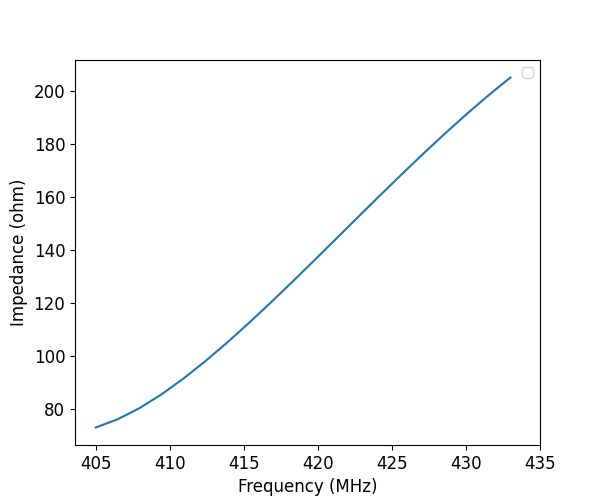
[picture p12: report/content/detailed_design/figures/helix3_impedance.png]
    
    \caption{Simulated Helical Antenna Impedance ($f_c = \SI{550}{MHz}$, $G_\lambda = 0.7$)}
    \label{fig:helix3_impedance}
  \end{minipage}
  \begin{minipage}{.49\textwidth}
    \centering
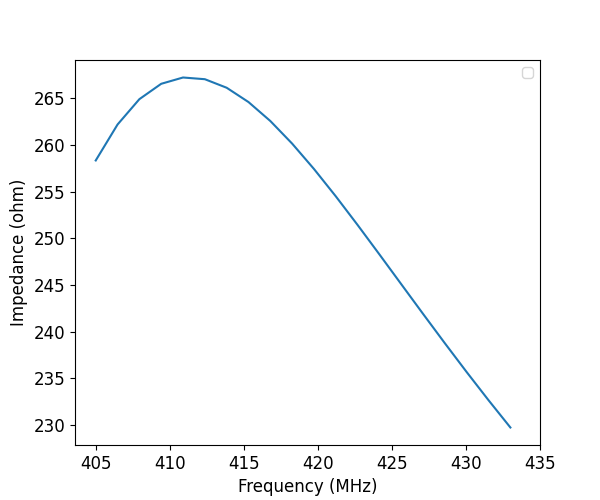
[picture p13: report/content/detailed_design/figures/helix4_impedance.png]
    
    \caption{Simulated Helical Antenna Impedance ($f_c = \SI{510}{MHz}$, $G_\lambda = 0.6$)}
    \label{fig:helix4_impedance}
  \end{minipage}
\end{figure}

\begin{figure}[!htb]
  \begin{minipage}{.49\textwidth}
    \centering
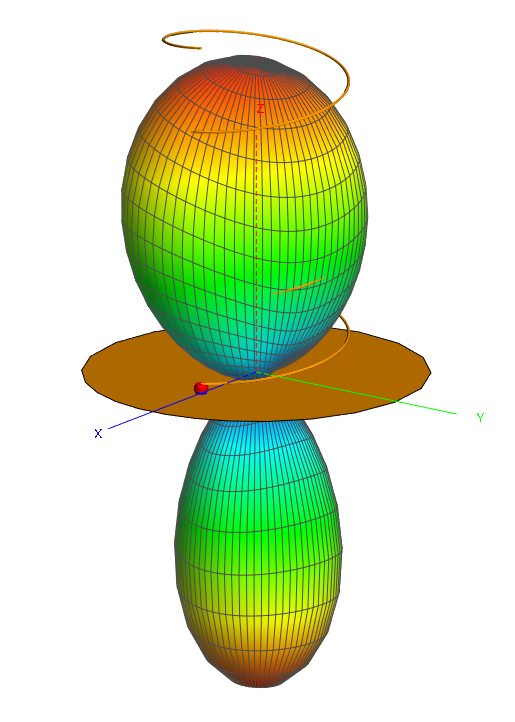
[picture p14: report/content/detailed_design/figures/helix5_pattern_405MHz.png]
    
    \caption{Simulated Helical Antenna Pattern without Cup at $f=\SI{405}{MHz}$ ($G_\lambda = 0.6$, $f_c=\SI{510}{MHz}$)}
    \label{fig:helix5_pattern_405MHz}
  \end{minipage}
  \begin{minipage}{.49\textwidth}
    \centering
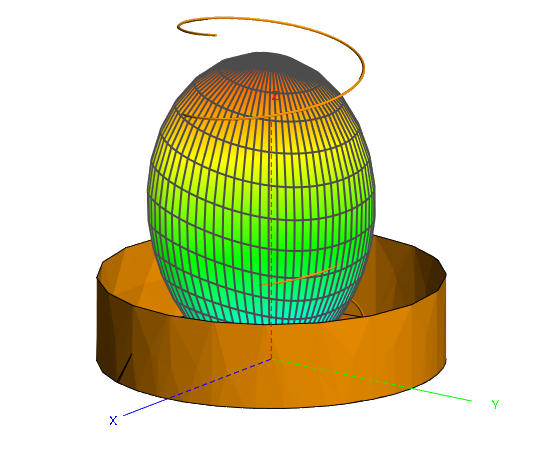
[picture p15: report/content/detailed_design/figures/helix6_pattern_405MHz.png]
    
    \caption{Simulated Helical Antenna Pattern with Cup at $f=\SI{405}{MHz}$ ($G_\lambda = 0.6$, $f_c=\SI{510}{MHz}$)}
    \label{fig:helix6_pattern_405MHz}
  \end{minipage}
\end{figure}

However, after analysing the input impedance for $G_\lambda = 0.7$ with this centre frequency (shown in Figure \ref{fig:helix3_impedance}) it is clear that broadband matching would be difficult, due to the drastic change in impedance near the lower end of the spectrum. In order to ease matching, a lower centre frequency should ideally be used, to move the input impedance at 405 MHz and at 433 MHz closer together. This will, however, require either a larger ground plane, or a cupped ground plane (discussed further on). Unfortunately, FEKO does not allow for an optimisation goal that depends on two frequencies. Therefore, an iterative approach was used to find the centre frequency which minimizes the impedance difference. 

The resulting centre frequency was found to be around $f_c = \SI{510}{MHz}$ at $G_\lambda = 0.6$ ($\approx \SI{350}{mm}$), with a band impedance between $\SI{230}{\ohm}$ and $\SI{260}{\ohm}$ (shown in Figure \ref{fig:helix4_impedance}).

Since the mount can support a larger weight than the 3 turn coil, it was decided to experiment with a larger turn count (i.e. $n=4$), both for increased directivity/performance, and to potentially cater for manufacturing imperfections, such as a thin aluminium foil ground plane, and any diversions from the ideal helical shape. It was found that, for small ground plane diameters, as the number of turns increased, the radiation pattern for $f = \SI{405}{MHz}$ was negatively affected. This is intuitive when referring to image theory, as the non-idealities due to the finitely-sized ground plane become more apparent as distance to the plane increases. It should be noted that the pattern at $f = \SI{433}{MHz}$ was not as adversely affected.

The ground plane was therefore cupped, and the results observed. At $G_\lambda = 0.6$, a cup height equal to 1 helical turn was found to greatly improve the radiation pattern. This is shown in Figures \ref{fig:helix5_pattern_405MHz} and \ref{fig:helix6_pattern_405MHz}. The gain, however, was not as drastically affected.

It was therefore decided that the antenna would initially be built with a large ground plane and higher number of turns. Then, after measurement results and protocol implementation, the ground plane would be decreased appropriately to fit onto the mount. If time allows, and it is deemed necessary, a cup will then be added to the ground plane, to improve the pattern and antenna performance, and cater for the radiosonde link. The final model parameters are then $D = \SI{187.1}{mm}$, $S = \SI{88.2}{mm}$, $n = 4$, and $G = \SI{350}{mm}$.

\subsection{Matching}
Impedance matching should be done if the helical antenna is to be fed by a $\SI{50}{\ohm}$ coaxial cable. It was decided to match the antenna to the custom link's frequency of $f = \SI{433}{MHz}$ using the strip method mentioned in Section \ref{sec:helical_matching} for an uncupped ground plane. The FEKO model for the strip is shown in Figure \ref{fig:helix7_model}.

\begin{figure}[!htb]
  \begin{minipage}{.4\textwidth}
    \centering
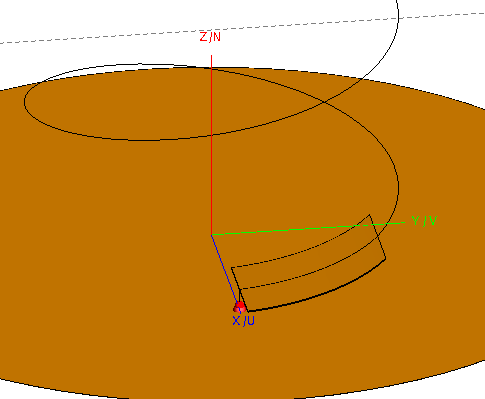
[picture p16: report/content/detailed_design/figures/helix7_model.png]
    
    \caption{Helical Antenna with Matching Strip Model}
    \label{fig:helix7_model}
  \end{minipage}
  \begin{minipage}{.58\textwidth}
    \centering
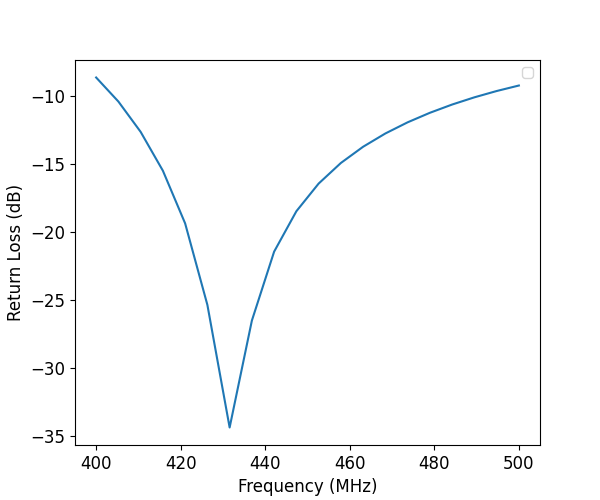
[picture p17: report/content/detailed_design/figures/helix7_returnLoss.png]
    
    \caption{Simulated Helical Antenna Return Loss vs Frequency}
    \label{fig:helix7_returnLoss}
  \end{minipage}
\end{figure}

According to literature \cite{textbook-helicalAntenna}, the strip is recommended to be relatively flat, and extend for approximately the first quarter turn. Its pitch angle was therefore chosen to be half that of the full helix, and it was chosen to extend for $0.15$ turns. The unknown parameters for the strip are then its height above the ground plane (also the height of the coaxial pin), and its strip width. The FEKO optimiser was used to optimise these two parameters for a minimum return loss. The resulting return loss as a function of frequency is shown in Figure \ref{fig:helix7_returnLoss}. The resultant mismatch loss is close to 0 dB at the target frequency, and 0.451 dB at 405 MHz. The final antenna parameters can be found in Table \ref{tab:helicalParameters} in the appendix. The simulated antenna gain was 7.5 dBi, resulting in a final designed link margin of 12.8 dB. The simulated beamwidth was 75 degrees, was is much larger than the required \SI{28}{^\circ}.

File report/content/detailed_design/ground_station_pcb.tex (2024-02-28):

\graphicspath{{./figures}}

\section{Ground Station PCB}
\subsection{Circuit Design}
For the ground station schematic, ``typical application" circuits found in component datasheets were mostly used. The final schematic can be found in Appendix \ref{sec:appendix_gs_schematics}.

\subsubsection{Motor Drivers}
The L6219 drivers require a reference voltage to set the maximum current. According to the datasheet \cite{datasheet-L6219}, a peak current of $I_{max} = 10 \times \frac{V_{ref}}{R_s}$ in mA is used. Since the recommended value of $R_s = \SI{1}{\ohm}$ is being used, $I_{max} = 10 \times V_{ref}$ mA. Since the motors allow up to 500 mA per winding, a current value of $I_{max} = \SI{475}{mA}$ is chosen to prevent damage. Therefore, $V_{ref} = \SI{4.75}{V}$, which can be implemented with a voltage divider. Setting the upper resistor $R_1 = \SI{1}{\kilo \ohm}$ results in $R_2 \approx \SI{20}{\kilo \ohm}$, as shown in the schematic. The disadvantage of this method is that the maximum current cannot be controlled dynamically. The reference can be replaced with a DAC from the MCU if more control is required.

\subsubsection{Connectors}
The RA-02 RF module states that not all data pins are necessary. Further, it was assumed that there may be some errors in the original design. A male header was therefore provided for unused GPIO pins, to allow for flexibility once the PCB was manufactured.

\subsection{PCB Layout}
A 2-layer stackup was decided on, since the in-house PCB machine has a 2-layer limitation, and it is desireable to manufacture the board as early as possible. The final PCB was designed in KiCAD. The layout is shown in Appendix \ref{sec:appendix_gs_pcb_design}. Female headers were used for most of the modules, since development boards were being used. Two PCB pours were exposed below the voltage regulators to act as a heat sink for added dissipation.

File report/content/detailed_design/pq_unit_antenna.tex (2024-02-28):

\graphicspath{{./figures}}

\section{PocketQube Unit Antenna}
\subsection{Mechanical Considerations}
Since the system is constrained close to the 433 MHz band (due to the radiosonde link), the wavelength of interest is relatively large (693 mm), and one half of a half-wavelength dipole is around 173 mm. Special consideration would be needed to fit this onto the planned PocketQube length of 150 mm. For the planned prototype balloon satellite launch, it is therefore decided to design a half-wavelength dipole, and allow it to simply protrude out the ends of the PocketQube housing from launch. Recommendations for future projects are given in Section \ref{sec:future_work} (such as designing a deployable antenna).

\subsection{Simulation Design and Matching}
A simple 1.5 mm metal wire will be used for the dipole due to its availability, which will be fed by a coaxial cable. The design parameters for the dipole are $L_\lambda$ (the total dipole length relative to lambda), $F_{\textnormal{gap}}$ (the gap distance of the feed), and $F_{length}$ (the length of the feed). A fixed gap distance of $F_{\textnormal{gap}} = \SI{5}{mm}$ was decided on, as it was assumed to not have a large impact on the results if it kept sufficiently small.

\begin{figure}[!htb]
  \begin{minipage}{.38\textwidth}
    \centering
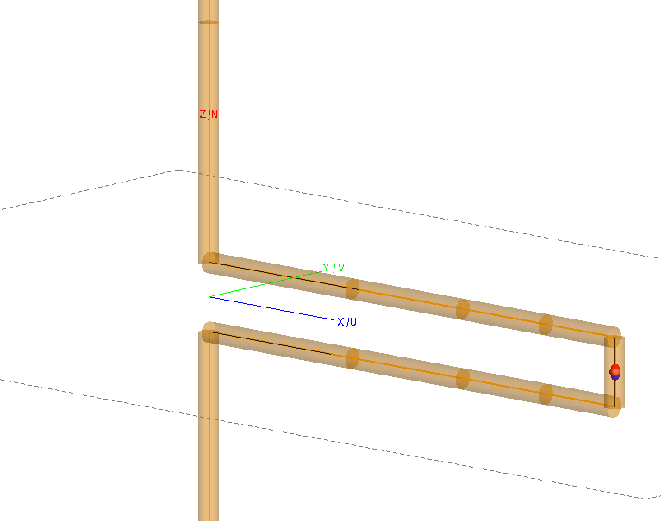
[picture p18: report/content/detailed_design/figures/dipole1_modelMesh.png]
    
    \caption{Dipole Model}
    \label{fig:dipole1_modelMesh}
  \end{minipage}
  \begin{minipage}{.6\textwidth}
    \centering
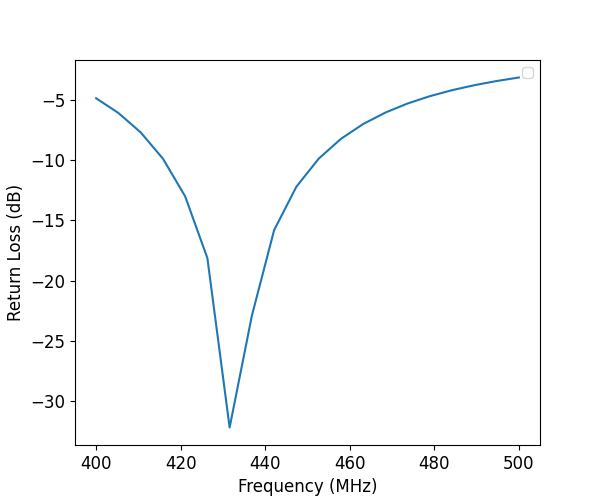
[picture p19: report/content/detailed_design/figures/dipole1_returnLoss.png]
    
    \caption{Simulated $0.45 \lambda$ Dipole Return Loss vs Frequency}
    \label{fig:dipole1_returnLoss}
  \end{minipage}
\end{figure}

The FEKO model in Figure \ref{fig:dipole1_modelMesh} was used. The optimiser was used to calculate the optimal dipole length and feed length that would minimize the return loss for $f = \SI{433}{MHz}$ at a feed impedance of $\SI{50}{\ohm}$. The resultant parameters are found to be $L_\lambda = 0.45$ ($L = \SI{312}{mm}$) and $F_{\textnormal{length}} = \SI{39.0}{mm}$. The optimised return loss as a function of frequency is shown in Figure \ref{fig:dipole1_returnLoss}. The radiation pattern was found to be the classic ``donut" shape, with a maximum directivity of 2.1 dBi.

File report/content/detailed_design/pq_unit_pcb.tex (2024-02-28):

\graphicspath{{./figures}}

\begin{figure}[!htb]
  \centering
  \begin{minipage}{.46\textwidth}
    \centering
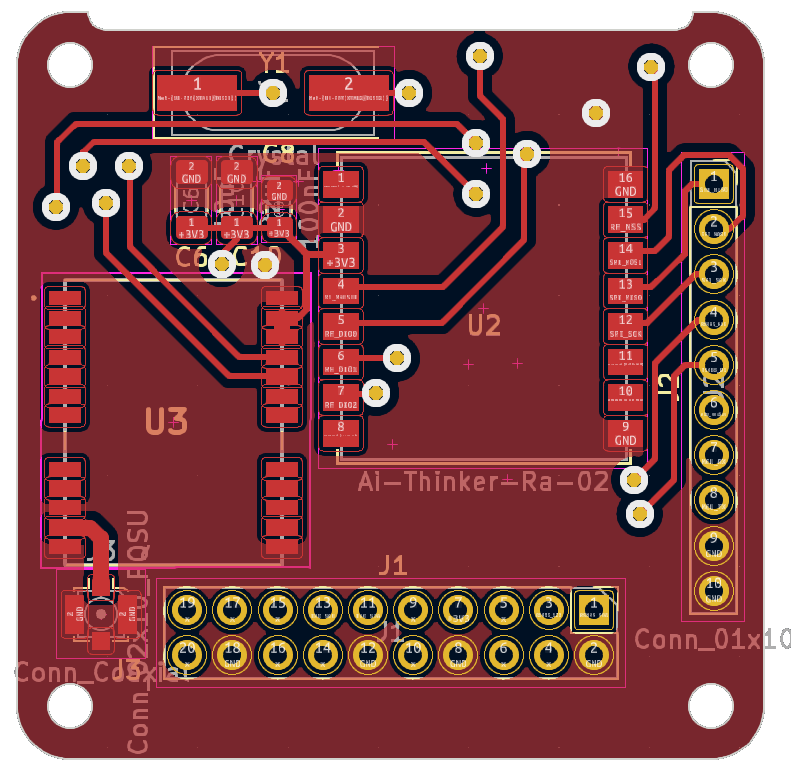
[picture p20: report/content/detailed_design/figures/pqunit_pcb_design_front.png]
    
    \captionof{figure}{PocketQube Unit PCB Design (Front)}
    \label{fig:pqunit_pcb_design_front}
  \end{minipage}
  \begin{minipage}{.46\textwidth}
    \centering
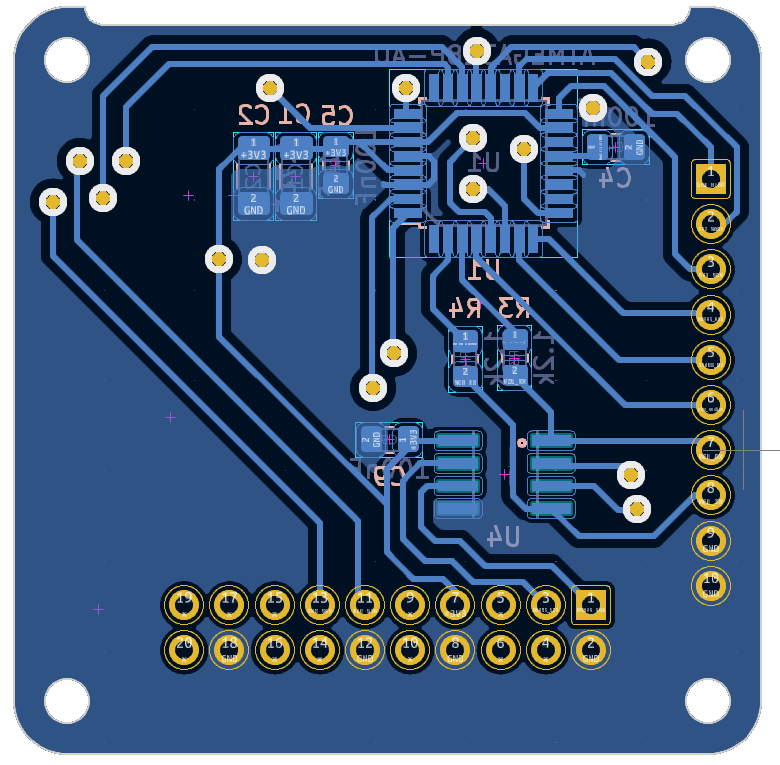
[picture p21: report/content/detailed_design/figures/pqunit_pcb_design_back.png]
    
    \captionof{figure}{PocketQube Unit PCB Design (Back)}
    \label{fig:pqunit_pcb_design_back}
  \end{minipage}
  \end{figure}

\section{PocketQube Unit PCB}
\subsection{Circuit Design}
For the circuit design, the Arduino Nano schematic \cite{design-arduinoNano} was consulted as a reference. The pins needed to flash the MCU were exposed directly, instead of integrating a USB connection, for simplicity. The final schematic can be found in Appendix \ref{sec:appendix_pq_schematic}.

\subsubsection{RF and GPS Modules}
Since the RA-02 RF module has a u.FL connector onboard, no considerations need to be taken with respect to impedance matching. The ATGM332D GPS module, however, directly exposes its RF input via one of its SMD pins. The higher L1 GPS band operates around 1575.42 MHz, which is a wavelength of $\frac{3e8}{1575.42e6} = \SI{190}{mm}$. The ``critical length" (the length at which reflections can be ignored) is therefore around \SI{19}{mm}. If the module-antenna trace length is kept shorter than this, impedance matching will not be necessary.

\subsection{PCB Layout}
It was decided to use a 2-layer board, due to the low component count. Although impedance matching is not necessary for the GPS module, it is still desirable to control the trace impedance as much as possible. However, a 50-ohm trace on a 2-layer board is around $\SI{2.8}{mm}$ (determined using a microstrip impedance calculator). This is much larger than the GPS module pad sizes. The trace was therefore made as wide and as short as possible. The final PocketQube PCB is shown in Figures \ref{fig:pqunit_pcb_design_front} and \ref{fig:pqunit_pcb_design_back}.

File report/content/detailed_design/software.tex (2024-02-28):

\graphicspath{{./figures}}

\section{Software}

\subsection{Classes}
The Arduino framework will be used, as well as a custom C++ library for re-usability across GS and PQ code. Tables \ref{tab:gpsUML} to \ref{tab:groundStationUML} in the appendix describe expected class functionality. Although the CSP protocol was considered, it was decided to rather develop a simple ASCII protocol between the PQ and GS, encapsulated in the \textit{link} class. The link class was designed to cater for downlink telemetry, but can easily be expanded on should satellite commands be required. The \textit{PqTnc} (PocketQube Terminal Node Controller) and \textit{PqUnit} classes were designed as singleton classes for the GS and PQ respectively. A serial protocol titled \textit{SUNCQ} was drawn up for the PqTnc-to-host communication and can be found in Appendix \ref{sec:appendix_suncq}.

\subsection{Tracking}
For path tracking, it is decided to store data in the TNC object on the ESP32 itself, instead of streaming it from the host computer. This is so that the host can be disconnected, and the payload will still be tracked. The tracking algorithm which caters both for open-loop and closed-loop methods is depicted in Figure \ref{fig:trackingAlgorithm}.

\begin{figure}[!htb]
  \centering
  
  \caption{Tracking Algorithm Flow Diagram}
  \label{fig:trackingAlgorithm}
\end{figure}

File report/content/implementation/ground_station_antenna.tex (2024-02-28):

\graphicspath{{./figures}}

\section{Ground Station Antenna}

The initial helical antenna build is shown in Figure \ref{fig:gsAntennaOriginal}. 2.5 mm stranded copper wire was used due to its flexibility and availability. A cardboad ground plane wrapped in aluminium foil was used due to its lightweight nature. Further, a strip of harder aluminium tin was taped to the wire for the matching strip. Initially, the strip was over-sized, and more turns than necessary were used. A female panel-mounted SMA connector was mounted using bolts, and the antenna wire was soldered to the protruding pin. The coiled wire is mechanically supported by a central PVC pipe and wooden dowels. Markings on the pipe were used to dimension the antenna. The materials were sized to provide stability, but not exceed the maximum torque limitations of the motors. The final antenna weight was measured at 344 g, giving a worst-case mass-distance product of $\SI{344}{g} \times \frac{\SI{45}{cm}}{2} \approx \SI{0.08}{kg \cdot m}$, which is under the maximum of $\SI{0.2}{kg \cdot m}$. After initial testing, the matching strip was cut to size, a circular trapezoidal cut-out was made to support a lower elevation angle, and the number of turns was set to $n=4$. The system was eventually mounted onto a tripod, and a final photo of the full ground station out in the field is shown in Figure \ref{fig:gsTripod}.

\begin{figure}[!htb]
  \begin{minipage}{.55\textwidth}
    \centering
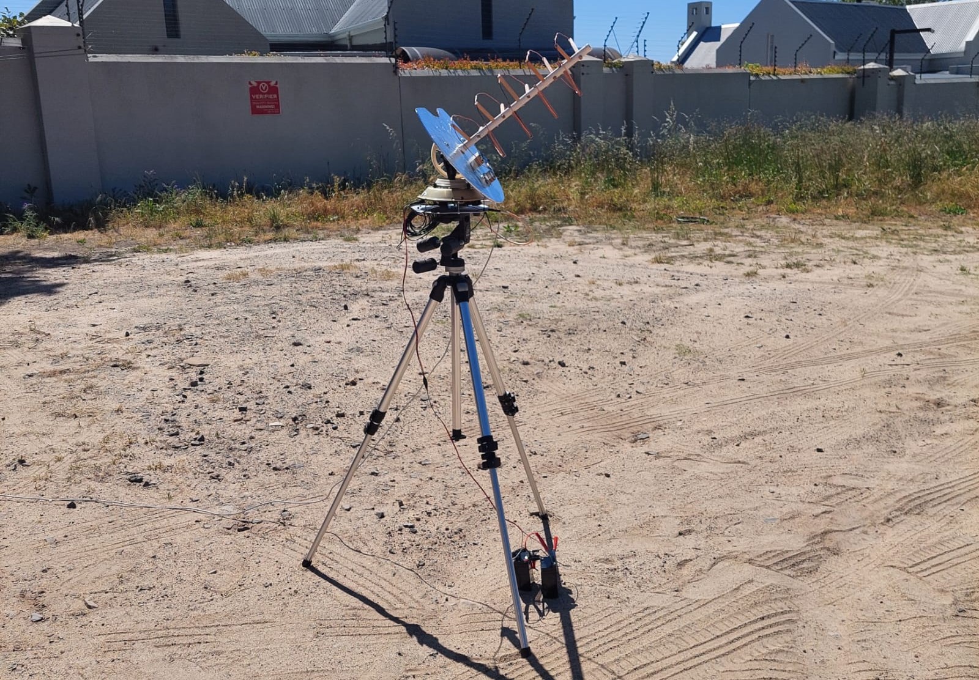
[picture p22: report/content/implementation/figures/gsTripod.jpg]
    
    \caption{Ground Station Mounted on a Tripod}
    \label{fig:gsTripod}
  \end{minipage}
  \begin{minipage}{.44\textwidth}
    \centering
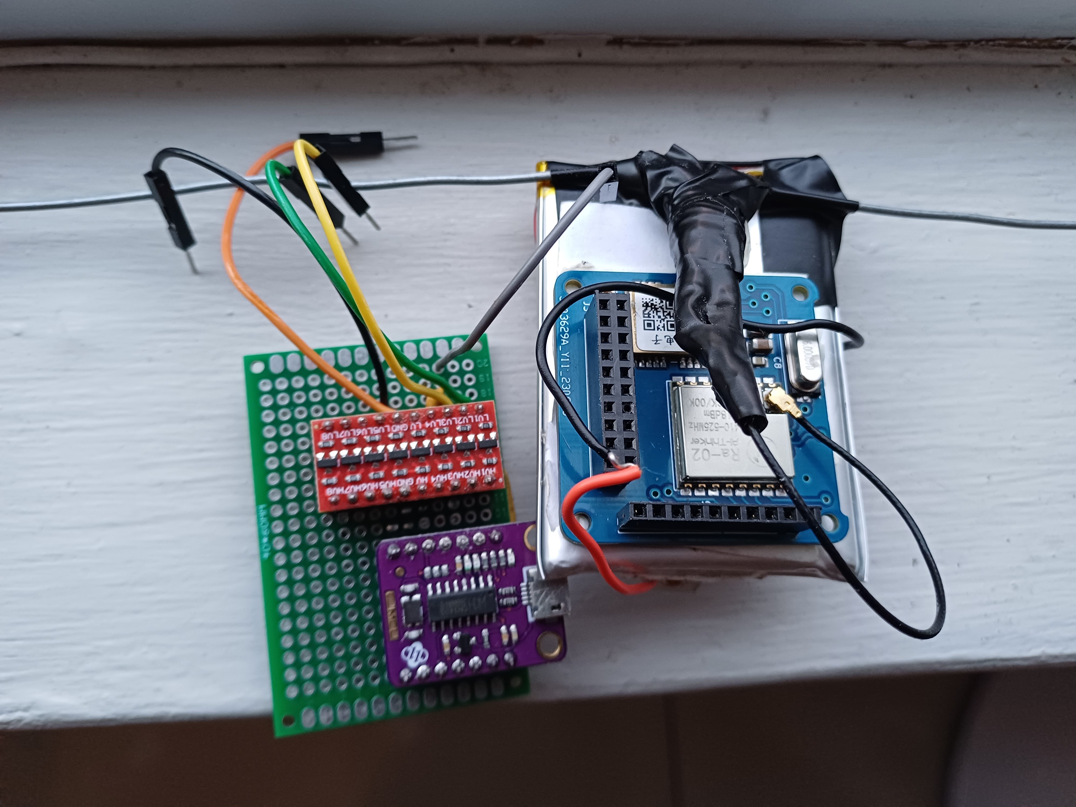
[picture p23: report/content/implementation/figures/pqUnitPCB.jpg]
    
    \caption{PQ Unit (front) [right] and programmer [left]}
    \label{fig:pqUnitPCB}
  \end{minipage}
\end{figure}

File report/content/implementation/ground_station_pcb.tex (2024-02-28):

\graphicspath{{./figures}}

\section{Ground Station PCB}

The ground station PCB was manufactured in-house. A figure of the PCB with components assembled, as well as a small helical antenna attached for initial development, and a monopole GPS antenna, is shown in Figure \ref{fig:groundStationPCB}. Some additional wired connections were made due to layout errors. A list of errata can be found in Appendix \ref{sec:appendix_pcb_errata}.

\begin{figure}[!htb]
  \begin{minipage}{.49\textwidth}
    \centering
    
    \caption{Ground Station PCB Implementation}
    \label{fig:groundStationPCB}
  \end{minipage}
  \begin{minipage}{.49\textwidth}
    \centering
    
    \caption{Ground Station Initial Antenna Implementation}
    \label{fig:gsAntennaOriginal}
  \end{minipage}
\end{figure}

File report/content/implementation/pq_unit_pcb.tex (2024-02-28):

\graphicspath{{./figures}}

\section{PocketQube Unit PCB}
Unfortunately, not enough prototypes were ready for an end-project balloon launch. The power section was therefore implemented using large but readily available converters/regulators. In a final launch, this would either be replaced by the EPS, or a low drop-out voltage regulator. The PQ unit PCB was ordered through an external supplier. In order to begin initial development and testing, an Arduino Nano breadboard prototype was created, as shown in Appendix \ref{sec:appendix_pq}. Since the Nano has the same MCU as the designed PCB, the developed software could then simply be flashed onto the PQ unit. The final module is shown in Figures \ref{fig:pqUnitPCB} and \ref{fig:pqUnitPower}. As noted in the appendix errata, the crystal's loading capacitors were mistakingly left out. The MCU's internal 8 MHz clock was therefore used, however was badly calibrated, and resulted in GPS software serial communication initially not working. This was fixed by setting the OSCCAL register appropriately. The board was first bootloaded with an Arduino Nano, and then the programmer circuit in Figure \ref{fig:pqUnitPCB} was developed to flash the board via UART. The programmer consists of a CH340 USB-to-serial module, a reset RC filter, and a $\SI{3.3}{V}$ to $\SI{5}{V}$ level converter (since the PocketQube PCB is designed to run at $\SI{3.3}{V}$). The board and dipole antenna was mounted onto the 2000 mAh LiPo battery. The power section consists of a LiPo charger, a boost converter module, and a $\SI{3.3}{V}$ linear voltage regulator circuit.

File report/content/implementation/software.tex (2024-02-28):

\graphicspath{{./figures}}

\begin{figure}[!htb]
  \begin{minipage}{.45\textwidth}
    \centering
    
    \caption{PQ Unit Antenna Implementation}
    \label{fig:pqAntenna}
  \end{minipage}
  \begin{minipage}{.49\textwidth}
    \centering
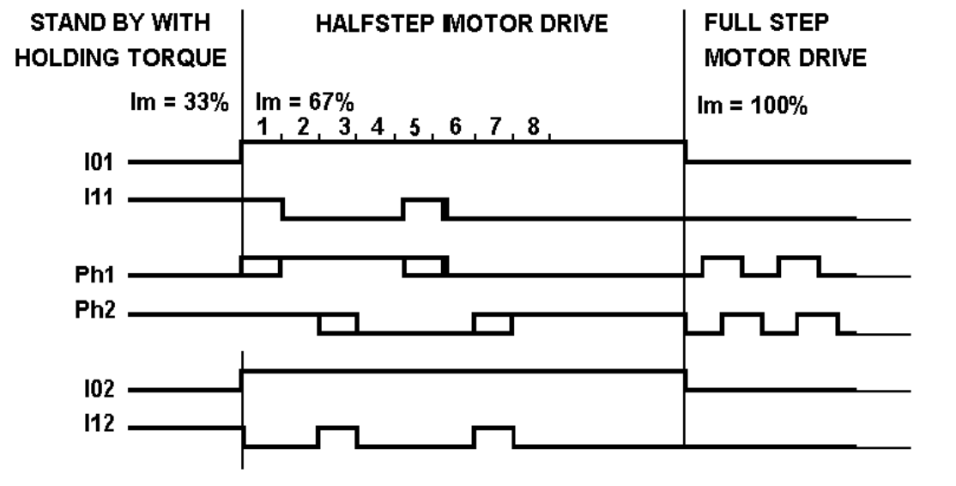
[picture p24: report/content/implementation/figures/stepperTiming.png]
    
    \caption{Stepper Motor Timing Diagram \cite{datasheet-L6219}}
    \label{fig:stepperTiming}
  \end{minipage}
\end{figure}

\section{Software}
All code is available at \url{https://github.com/gvcallen/pqcom/tree/main/code}.

\subsection{Mount Control}
The motors were setup in half-stepping mode, as shown in Figure \ref{fig:stepperTiming}, implemented using an array. Since both axes on the mount are dependent (see Figure \ref{fig:antennaMount}), the two-axis mount requires some relatively involved control. Elevational variation is straight-forward, as the azimuthal motor (controlled by Gear C) can be held fixed, and the elevation motor (Gear D) stepped accordingly. For azimuthal variation, if the elevation motor is held fixed, rotating the azimuthal motor causes the mount to also change in elevation, which must be compensated for (demonstrated in Appendix \ref{sec:appendix_mount_rotation}). The formulae to do this can be found in Appendix \ref{sec:appendix_mount_control}. To smoothly step both motors simultaneously, speeds are then set according to the ratio of the number of azimuthal and elevation motor steps to do.

\subsection{Pointing}
A small library titled \textit{wgs84} was used for the Mercator projection, with Cape Town as the origin. This allows a pointing vector to be determined, which is passed as the mount's boresight (where it is converted to azimuth-elevation co-ordinates). Unfortunately, the IMU (MPU-9250) was found to be counterfeit and lacked a magnetometer. The constraint was therefore made that a dead-reckoning fix to face magnetic north will be done. The angle between the zero sensor and magnetic north was therefore used as a reference input.

\subsection{Radio and GPS}
Existing Arduino libraries \textit{RadioLib} and \textit{TinyGPSPlus} were initially used for communication with the LoRa module and GPS module respectively. It was later found, however, that \textit{RadioLib} was too large in program size for the Atmega328, and it was therefore replaced with \textit{LoRaLib}, a smaller alternative.

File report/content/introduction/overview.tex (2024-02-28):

\graphicspath{{./figures}}

\section{Overview}

This project aims to design and implement a wireless communication system for a miniaturised satellite called a \textit{PocketQube} (PQ). The PocketQube standard was created to define physical and electronic requirements for so-called ``nano-satellites'', with the goal of easy integration of various sub-modules into one physical enclosure.

Nano-satellites can either be placed into orbit, or attached to a \textit{high-altitude balloon}. One common use-case of these balloons is to collect sensory information from the atmosphere, such as temperature and humidity readings. The goal of this project is to design a system that can be used in a balloon launched from the Saldanha Air Field, which may ultimately be done by the Stellenbosch Engineering department.

\begin{figure}[!htb]
  \begin{minipage}{.49\textwidth}
    \centering
    
    \caption{A High-Altitude Balloon Carrying a Nano-Satellite Payload \cite{site-cyberBalloonLaunch}}
    \label{fig:balloonSat}
  \end{minipage}
  \begin{minipage}{.49\textwidth}
    \centering
    
    \caption{A CAD Model of a Stellenbosch PocketQube Enclosure \cite{standard-pqsu}}
    \label{fig:pq_enclosure}
  \end{minipage}
\end{figure}

A satellite communication system includes both a ground station (GS), as well as a module on the satellite itself. The aim of this project is to establish a minimal prototype for both of these systems, so that future projects can refine the developed sub-systems. In this report, general system requirements are first listed, and a problem statement is drawn up. Then, a literature review is conducted to gather background information in the fields of interest. This includes an overview of the PocketQube standard, antenna theory, satellite tracking, and telecommunication theory. A systems level design is then done, which is followed by a more detailed design. Finally, the system is implemented and tested; the results are discussed; and potential improvements and work for future projects are listed.

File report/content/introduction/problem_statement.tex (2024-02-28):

\graphicspath{{./figures/}}

\section{Problem Statement}

The initial problem statement provided was simply to design a communication system for a \mbox{PocketQube}, with focus on the ground station. As this is relatively broad, investigation of both existing balloon-satellite systems, as well as the launch for this specific PocketQube, was done. An additional requirement that the GS should also be capable of receiving information from commercial \textit{radiosondes} (atmospheric telemetry devices) was also given. The specifications of existing radiosondes is therefore used as a reference, both for the new system's requirements, and as a consideration for system integration.

\begin{figure}[!htb]
  \centering
  
  \caption{Predicted Balloon Path and Distances}
  \label{fig:balloon_path}
\end{figure}

High-altitude balloons can drift to a height as much as 30 km above sea level, and can drift as far as 200 km from launch \cite{site-weatherWeatherBalloons}. As mentioned, this project's launch is planned to be near Saldanha Airfield. Using the \textit{HabHub} path predictor \cite{site-habHub}, on a day where the balloon travels far in-land, a launch from the airfield results in the path as in Figure \ref{fig:balloon_path}. From Cape Town, this is a maximum straight line distance of around 115 km. 

A ground station should maintain a reliable wireless link with a satellite to enable continuous communication and real-time telemetry. Since most radiosondes are simply uni-directional ``downlink" devices, this should be a priority. The GS should also, however, be capable of bi-directional communication, in order to issue commands to the satellite.

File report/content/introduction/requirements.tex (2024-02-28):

\section{Requirements}

From the information listed in the problem statement, and after supervisor consultation, slightly more specific user requirements are gathered and listed:
\begin{enumerate}
    \item The GS should be capable of receiving continuous data wirelessly from the PQ and the radiosonde. The PQ should be theoretically capable of responding to commands from the GS.
    \item The communication link should be maintained throughout the predicted path covered in Figure \ref{fig:balloon_path}
    \item The PQ unit should remain operational for at least the launch time of the predicted path, which is 2 hours 25 minutes. To cater for longer flights, a goal of 3 hours is set.
    \item The PQ unit should conform to the \textit{SU-modified} PQ9 standard (listed in Appendix \ref{sec:appendix_pqsu}), and integrate with other prototype units. This standard is here-on referred to as \textit{PQSU}.
    \item The GS electronics should integrate into an existing antenna mount, which has been provided by the E\&E Department.
\end{enumerate}

The system will undergo a \textit{flight-readiness review} to determine if it has met the requirements before launch. Although the GS could be placed closer to the launch location if the range requirement is not met (while affecting the communication time) this should only be used as a last resort. Further, as the project progresses, if supporting greater distances ($> 200$ km) will not significantly increase the time, complexity, or cost of the system, it could be catered for as an expansion to the core requirements. It should be noted, however, that the nature of this project (a system prototype) means that such optimisations should not be made a priority.

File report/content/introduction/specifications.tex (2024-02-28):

\graphicspath{{./figures}}

\section{Specifications}

In order to define a more detailed list of specifications, further calculations should be done. Balloon satellites rise at a vertical speed of around 20 km/h, and safely fall at around 35 km/h after bursting if a parachute is used \cite{site-weatherWeatherBalloons}. The predicted flight path in Figure \ref{fig:balloon_path} shows a travelled horizontal distance of about 60 km in 40 minutes after the balloon bursts, resulting in a horizontal speed of 90 km/h. A speed of around 100 km/h will be designed for, allowing slightly faster fall speeds.

At a maximum height of 30 km, a calculator reveals that the horizon is around 600 km \cite{site-normalHorizon}. The GS antenna could therefore be placed at sea level if communication is only required near maximum altitude. If the balloon should instead be tracked within one minute after launch (300 metres), then a radar horizon calculator reveals that the GS should be placed at an altitude no lower than 200 metres \cite{site-radarHorizon}, assuming no refraction.

Again referring to the predicted path, a maximum slant range of just over 115 km is obtained, noting that the balloon moves closer as it increases in altitude. For simplification, if the maximum speed (28 m/s) is assumed to occur perpendicular to the ground station at this maximum range, a turn-rate requirement of $t = \frac{v}{r} = \frac{28}{115000} \approx 0.015^\circ / s$ is obtained.

The PQSU standard includes 3.3 V and 5 V bus voltages. Since this is a prototype launch, there is risk of other units (e.g. the EPS) malfunctioning. A power connection is also needed for development. A simple battery system which matches the PQSU voltage should therefore be included, to be used both for testing, and potentially for deployment.

Both systems will require PCBs which are constrained in size. PQSU defines the dimensions of a PocketQube PCB i.e. 42 mm x 42 mm outer dimensions, whereas the ground station PCB is constrained to fit onto the provided mount with similar sizing as the previous PCB that was used with it, as shown in Appendix \ref{sec:appendix_gs_pcb_existing}. Lastly, the system should drive the stepper motors which are already provided with the antenna mount, and may make use of the existing zero-sensor. The following system-level specifications are therefore drawn up:
\begin{enumerate}
    \item The system should be capable of a slant range of 120 km.
    \item The GS should be capable of tracking at a turning rate of $0.015^\circ / s$, and the feasibility of various tracking methods (e.g. open vs closed loop) should be explored.
    \item The system should be designed to operate at a minimum baud rate of 4800 (which a typical radiosonde uses \cite{datasheet-iMet54}) and a target baud rate of 9600 (which is a typical satellite telemetry downlink speed \cite{paper-deployableAntenna}).
    \item The system should allow for radiosonde data to be retrieved in the meteorological band, between 400.05 and 406 MHz \cite{datasheet-iMet54}. This data is generally GFSK modulated.
    \item A single antenna should be used for both the custom and radiosonde link on the GS, to simplify the design. This antenna should therefore have a bandwidth in the range from 405 MHz up to the amateur radio band (433 MHz).
    \item A 100 mW equivalent transmit power restriction should be adhered to.
    \item The PQ unit should follow the PQSU and PQ9 standards, which stipulates: a 42 mm square outer PCB dimension; a 4 mm and 2 mm component height above and below respectively; and a 20-pin header interface, catering for RS-485 and I2C communication, and providing 3.3 V and 5 V power lines.
    \item The PQ unit should include a battery capable of lasting a minimum of 3 hours at nominal current draw.
    \item The GS PCB should integrate onto the existing antenna mount, which has a diameter of 198 mm, with equispaced mounting holes of 3 mm diameter.
    \item The GS should be mechanically steered using 4218S-15 bipolar stepper motors, which have a maximum current of 0.50 A per phase, and are driven at 24 V.
    \item The GS should provide a USB-C connection to allow a PC to monitor the telemetry data. This should be capable of receiving all data from the link in real-time.
\end{enumerate}

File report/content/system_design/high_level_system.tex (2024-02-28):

\graphicspath{{./figures}}

\section{High-Level System}
\subsection{Overview}
A complete high-level system block diagram illustrating the system-level decisions is shown in Figure \ref{fig:complete_system}. This project follows a waterfall methodology, where the functional components of the system are first considered; the system is designed using a top-down approach; and then the system is tested using a bottom-up approach. Since a large number of sub-systems are required on the ground-station, either IC \textit{modules} or simple \textit{reference designs} will form the basic building blocks of the system. Only if no modules or designs are found to meet the system requirements, will a more custom solution be developed. The ground station will be powered via +12 V from a battery, and the PocketQube will be powered from an on-board EPS (another PQ unit).

\begin{figure}[!htb]
    \centering
    
    \caption{High-Level System Diagram}
    \label{fig:complete_system}
  \end{figure}

\subsection{Tracking}\label{sec:tracking}
Further research shows that trajectory predictions for both the landing area and the dynamic altitude of a balloon can be up to 15-20 km inaccurate for a standard 2 hour flight \cite{paper-balloonTrajectoryAnalysis}. For the worst case, this is a total inaccuracy of $\sqrt{20^2 + 20^2} = \SI{28}{km}$. For the designed range of 120 km, this results in an angle inaccuracy of $360 \times \frac{28}{2 \pi \times 120} \approx 14^\circ$.

An antenna with a beamwidth of double this angle is therefore required, to ensure that the satellite is still within the beam, even when the antenna's boresight is pointing with worst-case open-loop accuracy. A Yagi-Uda antenna with a beamwidth of $28^\circ$ has a gain of around 17 dBi \cite{paper-yagiGainBeamwidth}. Using a common Si4311 FSK receiver's sensitivity of -104 dBm, an initial link budget can be estimated. If it is assumed that the link will use 100 mW (\SI{20}{dBm}) transmit power and the full 22 dBi gain, and experience 127 dB path loss at 120 km, then a 10 dB link margin is obtained.

Since the above link budget clearly indicates that open-loop tracking is feasible, it is decided to focus on this as the main tracking method. The ground station therefore requires at least a GPS connection; a means of determining true north (such as a magnetometer); and a means of uploading path data. The path data will be uploaded to the ground station via USB from a system computer. If time allows, direct GPS tracking will then be added as a method of ``closing the loop", and to improve pointing accuracy.

\subsection{Custom Link}
A half-duplex link will be designed. This is decided on due to the nature of the link itself (i.e. either downlink ``telemetry" or a simple command-response ``telecommand" pattern) and due to the added complexity which full-duplex would require (i.e. a dual frequency system).

For the given flight path, a goal of at least 9600 downlink baud rate will be designed for at the 120 km range, with LoRa being explored as the main modulation technique. This is chosen due to the high sensitivity it offers (which helps alleviate the need for a large, high-gain antenna), as well as the link speed it offers for reasonable bandwidth ($< \SI{500}{kHz}$). GFSK will be considered as a backup option, since it is well-established in literature. The 433 MHz amateur band (430 to 440 MHz) will be utilized.

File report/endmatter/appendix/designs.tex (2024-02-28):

% Designs
\chapter{Design}
\section{Power Calculations}
\begin{table}[!htb]
  \centering
  \renewcommand{\arraystretch}{1.2}
  \begin{tabular}{ |c|c|c|c| }
  \hline
  \textbf{Component}        & \textbf{Voltage}    & \textbf{Current}     & \textbf{Power}   \\
  \hline
  Motors                    & 24 V                & 0.5 A (x4)           & 48 W             \\ \hline
  Motor Drivers             & 5 V                 & 89 mA (x2)           & 890 mW           \\ \hline
  ESP32 Dev Board           & 5 V                 & 120 mA               & 660 mW           \\ \hline
  RA-02                     & 3.3 V               & 100 mA               & 330 mW           \\ \hline
  ATGM332D-5N31             & 3.3 V               & 25 mA                & 82.5 mW          \\ \hline
  MPU-9250                  & 3.3 V               & 3.7 mA               & 12.21 mW         \\ \hline
  \textbf{Total}            &                     &                      & \textbf{49.97 W}         \\ \hline
  \end{tabular}
  \caption{Ground Station Total Power Calculation}
  \label{tab:gs_component_consumption}
\end{table}

\begin{table}[!htb]
  \centering
  \renewcommand{\arraystretch}{1.2}
  \begin{tabular}{ |c|c|c| }
  \hline
  \textbf{Component}        & \textbf{Current}        & \textbf{Power (@ 3V3)}      \\ \hline 
  ATmega328                 & 12 mA                   & 39.6 mW                     \\ \hline 
  RA-02                     & 100 mA                  & 330 mW                      \\ \hline 
  ATGM332D-5N31             & 25 mA                   & 82.5 mW                     \\ \hline
  MAX485                    & 137.3 mA                & 1.0 mW                        \\ \hline
  \textbf{Total}            &                         & \textbf{453.1 mW}         \\ \hline
  \end{tabular}
  \caption{PocketQube Unit Component Power Consumption}
  \label{tab:pqunit_component_consumption}
\end{table}

\clearpage
\includepdf[scale=0.85,pages=1,offset=0mm -10mm,pagecommand=\section{Ground Station Schematic}\label{sec:appendix_gs_schematics}]{docs/gs_schematic}
\includepdf[scale=0.85,pages=1,offset=0mm -10mm,pagecommand=\section{PocketQube Unit Schematic}\label{sec:appendix_pq_schematic}]{docs/pq_schematic}

\section{Ground Station PCB}\label{sec:appendix_gs_pcb_design}
\begin{figure}[!htb]
  \centering
  
  \caption{Ground Station PCB Design (front)}
  \label{fig:gs_pcb_design_front}
\end{figure}
\begin{figure}[!htb]
  \centering
  
  \caption{Ground Station PCB Design (back)}
  \label{fig:gs_pcb_design_back}
\end{figure}
\clearpage

\section{PCB Errata}\label{sec:appendix_pcb_errata}
Ground Station PCB:
\begin{itemize}
  \item The zero-sensor JST pin connections were incorrect.
  \item ESP Pins IO1 and IO3 should be left free for UART communication. Nets M2\_IO1 and M2\_I11 are therefore moved to pins IO14 and IO12 respectively.
  \item ESP Pins IO34 and IO35 are input-only. Nets M1\_I01 and M1\_I11 are therefore moved to pins IO0 and IO16 respectively. In this case, GPS\_TX is no longer used, and pin 0 on-board the ESP module on the board must be soldered to directly.
  \item The ESP development board's footprint was sized slightly to wide, and should be narrowed to avoid having to bend the pins.
\end{itemize}

\noindent PocketQube Unit PCB:
\begin{itemize}
  \item The loading capacitors on the crystal oscillator were incorrectly left out. The 8 MHz clock was therefore used, however the capacitors should be added in order for a 16 MHz clock to be used.
\end{itemize}

\section{Ground Station Antenna}
\begin{table}[!htb]
  \centering
  \renewcommand{\arraystretch}{1.2}
  \begin{tabular}{ |c|c| }
  \hline
  \textbf{Parameter}                  & \textbf{Value}    \\
  \hline
  Diameter (D)                        & 187.1 mm          \\ \hline
  Turn Spacing (S)                    & 88.2 mm           \\ \hline
  No. of Turns (n)                    & 4                 \\ \hline
  Ground plane diameter (G)           & $> \SI{350}{mm}$  \\ \hline
  Strip height (sh)                   & 19.4 mm          \\ \hline
  Strip width (sw)                    & 77.7 mm           \\ \hline
  Strip length (sl)                   & 132 mm           \\ \hline
  Cup height, if used (ch)            & 88.2 mm           \\ \hline
  \end{tabular}
  \caption{Helical Antenna Final Parameters}
  \label{tab:helicalParameters}
\end{table}

\newpage
\section{Software}
\begin{table}[!htb]
  \centering
  \caption{GPS Class}
  \renewcommand{\arraystretch}{1.2}
  \begin{tabular}{ |c|c| }
  \hline
  \textbf{Function}        & \textbf{Description}    \\
  \hline
    getLocation()              & Return latitude, longitude and altitude \\
    getTime()                  & Return seconds since epoch \\
  \hline
  \end{tabular}
  \label{tab:gpsUML}
\end{table}

\begin{table}[!htb]
  \centering
  \caption{Radio Class}
  \renewcommand{\arraystretch}{1.2}
  \begin{tabular}{ |c|c| }
  \hline
  \textbf{Function}        & \textbf{Description}    \\
  \hline
    startTransmit(message)              & Transmit data (non-blocking i.e. with callback) \\
    startReceive()                      & Start listening to receive data (non-blocking i.e. with callback) \\
    getRssi()                           & Get signal strength \\
    getSnr()                            & Get signal-to-noise ratio \\
  \hline
  \end{tabular}
  \label{tab:radioUML}
\end{table}

\begin{table}[!htb]
  \centering
  \caption{Link Class}
  \renewcommand{\arraystretch}{1.2}
  \begin{tabular}{ |c|c| }
  \hline
  \textbf{Function}        & \textbf{Description}    \\
  \hline
  setTelemetryCallback(fn)                    & Set the ``telemetry sent/received" function  \\
  setTelecommandCallback(fn)                  & Set the ``telecommand received" function (\textit{Responder} only) \\
  \hline
  \end{tabular}
  \label{tab:linkUML}
\end{table}

\begin{table}[!htb]
  \centering
  \caption{StepperMotor Class}
  \renewcommand{\arraystretch}{1.2}
  \begin{tabular}{ |c|c| }
  \hline
  \textbf{Function}        & \textbf{Description}    \\
  \hline
    stepForward(numSteps)         & Blocking and non-blocking options \\
    saveZeroPosition()            & Used for calibration \\
    getPosition()                 & Used for open-loop feedback \\
    setSpeed()                    & Sets the delay between steps \\
    setCurrentMultiplier()        & Set the amount of current \\
  \hline
  \end{tabular}
  \label{tab:stepperMotorUML}
\end{table}

\begin{table}[!htb]
  \centering
  \caption{Mount Class}
  \renewcommand{\arraystretch}{1.2}
  \begin{tabular}{ |c|c| }
  \hline
  \textbf{Function}        & \textbf{Description}    \\
  \hline
    calibrate()                         & Calbrate the mount \\
    setAzimuthalElevation(az, el)       & Set the azimuthal and elevation angles \\
    setBoresight(boresightVec)          & Set the boresight pointing vector \\
  \hline
  \end{tabular}
  \label{tab:mountUML}
\end{table}

\begin{table}[!htb]
  \centering
  \caption{GroundStation Class}
  \renewcommand{\arraystretch}{1.2}
  \begin{tabular}{ |c|c| }
  \hline
  \textbf{Function}             & \textbf{Description}    \\
  \hline
    calibrate()                 & Calibrate the entire GS \\
    addEstimatedLocation(loc)      & Add an estimated input GPS location for open-loop tracking \\
    addKnownLocation(loc)          & Add a known GPS location for closed-loop tracking \\
  \hline
  \end{tabular}
  \label{tab:groundStationUML}
\end{table}

\section{Mount Calibration}\label{sec:appendix_mount_calibration}

The calibration procedure of the mount is described below:
\begin{itemize}
  \item Measure the elevation angles of the mount at both extremes.
  \item Measure the offset angle between the zero-sensor and the desired magnetic north location.
  \item Lookup the magnetic declination near the area of interest.
  \item Include the previous three values statically in the software code.
  \item Rest the mount on the side with the larger elevation angle.
  \item Face the mount towards magnetic north.
  \item Run the mount's software calibration procedure, which rotates in azimuth until the zero sensor is found; then in elevation (open-loop) until the start elevation angle is reached; and finally faces north using the magnetic declination and offset angle.
\end{itemize}

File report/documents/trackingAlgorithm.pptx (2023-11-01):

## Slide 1

Update Tracking
(run e.g. once per second)

Is the latest received GPS
co-ordinate less than 60 seconds old?

Yes

Set the pointing location to the received GPS location

Set the active instant to the next path instant while setting the previous path instant to the old active instant

Is the maximum angle that needs to be moved less than 5 degrees?

Set the pointing location to a time-based linear interpolation between the previous and current path instants

Finish

No

No

Is the current time later than the next path instant’s time?

Yes

Move to the pointing location

Yes

No

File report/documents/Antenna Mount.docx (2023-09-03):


Gear D

Gear C

Gear A

Gear B

Gear E

Pivot Axle

Centre Shaft

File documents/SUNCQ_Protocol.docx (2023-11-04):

# SUNCQ Protocol

## Description

This document defines the Stellenbosch University Node Control for Qubes (SUNCQ) protocol. It lays out the commands to communicate with a Stellenbosch University PocketQube Ground Station via a TNC. A TNC (Terminal Node Controller) is a serial interface system which allows for control over a ground station or radio. This protocol defines the messages to and from the TNC and the computer (referred to as the host). Its current implementation requires commands to not be sent more frequently than once every second. It was authored by Gary Allen, a 2023 E&E student.

## Commands

The following lists all commands from TNC to host and vica-versa. The command reservations are:

- 0x00 to 0x2F Host-to-TNC DO commands
- 0x30 to 0x5F Host-to-TNC SET commands
- 0x60 to 0x7F Host-to-TNC GET commands
- 0x80 to 0x9F TNC-to-Host STATUS replies
- 0xA0 to 0xCF TNC-to-Host DATA replies
- 0xD0 to 0xFE Reserved
- 0xFF Invalid

Code | Name | Function | Payload | Bytes | Comments
0x00 | RESET | Reset the system | - | 0
0x01 | CALIBRATE | Calibrate the system | - | 0 | Full calibration e.g. ground station and all sub-systems
0x02 | RETURN_TO_START | Return the system to its starting state. | - | 0 | The starting state is post-calibration.
0x03 | RETURN_TO_STOW | Return the system to its stow state. | | | The stow state is pre-calibration. Typically used before system shutdown
0x30 | SET_TNC_MODE | Enter a certain mode | See TNC_MODE | 1
0x31 | SET_TRACK_MODE | Set tracking mode | See TRACK_MODE | 1
0x32 | SET_PATH_DATA | Upload flight path data | CSV file. See Flight Path Data. | Any | The payload length is provided as the first 8 bytes.
0x33 | SET_TRACK_LOCATION | Set point direction, or add a received GPS location (depending on the track mode) | See Flight Path Data (pass only one entry)
0x34 | SET_TRACK_TARGET | Set the target to track | See TRACK_TARGET | 1 | Allows for the custom internal target, or any external target, to be tracked (in which case the internal receiver is disbable)
0x60 | GET_SIGNAL_RSSI | Get RSSI of the signal | - | 0
0x61 | GET_LOCATION | Get location of the ground station | Lat;Lng;Alt (f32;f32;f32) | 12
0x80 | TNC_TELEMETRY | Sent by the TNC to send telemetry to the host | See STATUS_CODE. | 1 | Status 0x00 is used as an “ACK” command.
0x81 | TNC_MESSAGE | Sent by the TNC to communicate a log message to the host. | char[] | Any | A newline character terminates the message
0xA0 | SIGNAL_RSSI | Response to GET_SIGNAL_RSSI | float | 4
0xD0-0xFE | RESERVED | Reserved | | | Reserved for future use
0XFF | INVALID | Invalid | | | An invalid command that can be used internally but never sent

## Details

#### TNC_MODE

Value | Description
0x00 | Normal mode
0x01 | KISS mode. This mode is exited using the KISS 0xFF command.

#### TRACK_MODE

The tracking mode is a combination flag i.e. multiple bits can be ORed together to specify that the payload must be tracked using multiple methods at once.

Value | Description
0x00 | No tracking. Mount can be moved by setting the pointing vector.
0x01 | Use uploaded GPS data
0x02 | Use received GPS data (from payload)
0x04 | Use signal strength, but only for an initial scan
0x08 | Use signal strength, with dynamic conical scanning

#### TRACK_TARGET

The tracking mode is a combination flag i.e. multiple bits can be ORed together to specify that the payload must be tracked using multiple methods at once.

Value | Description
0x00 | Internal
0x01 | External

#### STATUS_CODE

The following is a list of status codes that might be sent from the TNC to the host:

Value | Description
0x00 | Acknowledge
0x01 | Payload tracking unsuccessful/payload lost

#### Flight path data

Flight path data can be uploaded in the form of a little-endian binary stream (i.e. each field should be least significant byte first). The first field is a 2-byte number indicating the number of flight path instances to follow. Then, the fields below should be provided. Such a file can be generated by predicting a flight path at https://predict.sondehub.org/ , generating a CSV file, and then using the data to generated a binary stream. In the current implementation, only 200 entries are catered for – if longer flights are needed, then multiple streams should be set from the host intermittently. Time should be in Unix time (seconds since Epoch).

Name | Type
Time | uint64
Latitude | float32
Longitude | float32
Altitude | float32

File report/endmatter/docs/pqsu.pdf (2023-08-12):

## Pocketcube Mechanical Interface

Dirk Slabber, MEng | Electronic Systems Laboratory| Stellenbosch University

13/06/2023

* unless otherwise specified all measurements are to “The PocketQube Standard” [Issue 1, 7th of June, 2018], PQ9 and CS14 standard.


Figure 1- pocketcube structure | Figure 2- pocketcube bus layout

Physical Envelope


Figure 3-dimensions of the slot | Figure 4-90-degree pins

Please take care to not place components such that it will obstruct the 90-degree bus pins as well as the nuts that will be hold the slot in place around the four mounting holes. Components may project up to 8mm away from the board and still slot in with another board directly next to it.

Electrical Connection
Each slot is has twenty pins connected a bus in the main plate. Pin 1 is located top right on figure 3, pin 11 bottom right and so on. The suggested pinout on the bus is as follows:
1 | SDA | SDL | 11
2 | Ground | Ground | 12
3 | SDB | System Clock | 13
4 | User defined | 5V Switch 1 | 14
5 | Power source | 5V Switch 2 | 15
6 | 5V line | 3.3V Switch 1 | 16
7 | 3.3 line | 3.3V Switch 2 | 17
8 | Ground | Ground | 18
9 | User defined | PPS | 19
10 | User defined | User defined | 20

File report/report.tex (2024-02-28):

\documentclass[a4paper,12pt]{report}

% Global commands
\newcommand{\reportTitle}{
    \textcolor{black}{The Development of a PocketQube Satellite Communication System}
}

\newcommand{\reportSubtitle}{
    \textcolor{black}{}
}

\newcommand{\nameInitial}{
    \textcolor{black}{G. Allen}
}
\newcommand{\nameFull}{
    \textcolor{black}{Gary Allen\\23905093}
}

\newcommand{\stNumber}{
    \textcolor{black}{}
}
\newcommand{\myDate}{\textcolor{black}{\today}
}

% Page layout
\usepackage[left=2.5cm,right=2.5cm,top=2.5cm,bottom=2.5cm]{geometry}

% Figures
\usepackage[margin=\the\parindent,small,bf,sf]{caption}
\usepackage{graphicx}
\usepackage{pdfpages}
\setlength{\abovecaptionskip}{7.5pt}  % spacing above and below captions
\newcommand*{\WaterMark}[2][0.2\paperwidth]{\AddToShipoutPicture*{\AtTextCenter{\parbox[c]{0pt}{\makebox[0pt][c]{}}}}}
\usepackage{subcaption}

% Font and text
\usepackage[english]{babel}
\usepackage{microtype}
\usepackage{setspace}
\usepackage{lmodern}
\newcommand{\myemph}[1]{{\sffamily\bfseries#1}}
\sloppy
\onehalfspacing
\usepackage{siunitx}
\usepackage{lipsum}
% \RenewDocumentCommand{\chapterbelowskip}{}{\vspace*{0pt}}

% Headings
\usepackage[raggedright,sf,bf]{titlesec}
\titleformat{\chapter}[display] {\normalfont\bfseries}{}{0pt}{\Huge}
\titleformat{\chapter}[hang]{\Huge\bfseries}{\thechapter{. }}{0pt}{\Huge\bfseries}

% Table of contents
\makeatletter
\let\originall@chapter\l@chapter
\def\l@chapter#1#2{\originall@chapter{{\sffamily #1}}{#2}}
\makeatother
\let \savenumberline \numberline
\def \numberline#1{\savenumberline{#1.}}

% Mathematics
\usepackage[cmex10]{amsmath}
\usepackage{amssymb}
\usepackage{cancel}
\DeclareMathOperator*{\argmax}{arg\,max}
\newcommand{\T}{^\textrm{T}}
\newcommand{\tr}{\textrm{tr}}
\renewcommand{\vec}[1]{\boldsymbol{\mathbf{#1}}}
\newcommand{\defeq}{\triangleq}

% Tables
\usepackage{booktabs}
\usepackage{tabularx}
\usepackage{multirow}
\newcommand{\mytable}{
    \centering
    \small
    \renewcommand{\arraystretch}{1.2}
    }
\renewcommand{\tabularxcolumn}[1]{m{#1}}
\newcolumntype{C}{>{\centering\arraybackslash}X}
\newcolumntype{L}{>{\raggedright\arraybackslash}X}
\usepackage{makecell}

% Header and footer
\usepackage{fancyhdr}
\pagestyle{fancy}
\fancyhf{}
\renewcommand{\sectionmark}[1]{\markright{\normalsize \thesection.\ #1}}
\fancyhead[C]{\nouppercase{\textit{\rightmark}}}
\fancyhead[RO]{\thepage}
\fancyfoot{}
\setlength\headheight{14.5pt}
\renewcommand{\headrulewidth}{0pt}
\fancypagestyle{plain}{\fancyhead{}
                       \renewcommand{\headrulewidth}{0pt}
                       \fancyfoot[C]{\thepage}}

% Pseudo-code
\usepackage{algorithm}  % should go before \usepackage{hyperref}

% Table of contents and hyperlinks
\usepackage{hyperref}
\hypersetup{colorlinks=true,linktoc=all,citecolor=black,linkcolor=black}
\usepackage[nottoc]{tocbibind}

% Pseudo-code
\usepackage{algpseudocode}  % should go after \usepackage{hyperref}
\renewcommand{\thealgorithm}{\arabic{chapter}.\arabic{algorithm}} 
\captionsetup[algorithm]{labelfont={bf,sf},font=small,labelsep=colon}

% Bibliography
\usepackage{cite}  % automatically reorder inline citations
\bibliographystyle{IEEEtran}

% Fix titlesec issue
\usepackage{etoolbox}
\makeatletter
\patchcmd{\ttlh@hang}{\parindent\z@}{\parindent\z@\leavevmode}{}{}
\patchcmd{\ttlh@hang}{\noindent}{}{}{}
\makeatother
 \usepackage[normalem]{ulem}

\usepackage{subfiles}

% Document 
\begin{document}

% Front matter
\subfile{frontmatter/title_page}
\subfile{frontmatter/acknowledgements}
% \subfile{frontmatter/declaration}
\includepdf[scale=1.0]{frontmatter/docs/plagiarism_signed}
\subfile{frontmatter/abstract}
\pagenumbering{roman}
\tableofcontents
\listoffigures
\listoftables
\subfile{frontmatter/nomenclature}
\newpage
\pagenumbering{arabic}

% Contents
\subfile{content/content.tex}

% Bibliography
\bibliography{references}

% End matter
\appendix
\subfile{endmatter/appendix}

\end{document}

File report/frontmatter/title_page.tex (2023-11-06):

\graphicspath{{./figures/}}
\pagenumbering{Alph}

\begin{titlepage}
\begin{center}



\vfill

{\sffamily \bfseries \huge \reportTitle \par}

{\sffamily \bfseries \Large \reportSubtitle \par}

\vfill

{\large {\Large \nameFull} \\ \stNumber \par}

Report submitted in partial fulfilment of the requirements of the module
Project (E) 448 for the degree Baccalaureus in Engineering in the Department of Electrical
and Electronic Engineering at the University of Stellenbosch.

\vfill

\vfill
Supervisor: Dr A. Barnard

\vfill

\vfill

{\Large \myDate}
\end{center}
\end{titlepage}

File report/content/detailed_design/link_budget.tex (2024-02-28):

\section{Link Budget}

The link budget should now be estimated, and initial considerations for the ground station's base location should be made. Signal Hill in Cape Town is a viable location, and is easily accessible. At its distance of 114 km, however, one would need to be at a height of 950 m for communication from launch (due to the earth's curvature). Since the balloon would become visible at an altitude of $\SI{600}{m}$ from Signal Hill's $\SI{350}{m}$ height, this location is chosen. This allows communication 12 seconds after launch, if an ascent rate of $\SI{5}{m.s^{-1}}$ is assumed. A maximum elevation angle of $16.72^\circ$ at 30 km altitude should be considered.

\begin{table}[!htb]
  \begin{minipage}{.49\textwidth}
      \centering
      \renewcommand{\arraystretch}{1.2}
      \begin{tabular}{ |c|c| }
      \hline
      Transmitter Power             & 18 dBm                    \\ \hline
      Mismatch Loss                 & (0.5 dB)                 \\ \hline
      Transmission Line Loss        & (1 dB)                  \\ \hline
      Antenna Gain                  & 2.15 dB                   \\ \hline
      \textbf{EIRP}                 & \textbf{18.65 dBm}        \\ \hline
      \end{tabular}
      \caption{Link Budget - Satellite}
      \label{tab:link_budget_satellite}
  \end{minipage}
  \begin{minipage}{.49\textwidth}
      \centering
      \renewcommand{\arraystretch}{1.2}
      \begin{tabular}{ |c|c| }
      \hline
      Free space path loss (114 km) & 126.3 dB                  \\ \hline
      Atmospheric loss              & 0.22 dB                   \\ \hline
      Scintillation loss            & 0.37 dB                   \\ \hline
      Polarization Mismatch         & 3 dB                      \\ \hline
      \textbf{Total Loss}           & \textbf{129.89 dB}         \\ \hline
      \end{tabular}
      \caption{Link Budget - Channel}
      \label{tab:link_budget_channel}
  \end{minipage}
\end{table}

\begin{table}[!htb]
  \centering
  \renewcommand{\arraystretch}{1.2}
  \begin{tabular}{ |c|c| }
  \hline
  Antenna Gain                  & 2.15 dBi                \\ \hline
  Mismatch Loss                 & (0.5 dB)                \\ \hline
  Transmission Line Loss        & (1 dB)                  \\ \hline
  Receiver Sensitivity          & 119 dBm                 \\ \hline
  \textbf{GS Sensitivity}       & \textbf{119.65 dBm}     \\ \hline
  \end{tabular}
  \caption{Link Budget - Ground Station}
  \label{tab:link_budget_gs}
\end{table}

Notable configurations for the SX1278's sensitivity (the minimum receivable power level) are listed in Table \ref{tab:sensitivity_values}. The LoRa ``target bit rate" sensitivity value of -119 dBm (SF = 8 and BW = 500 kHz) is decided on, since it provides the 9600 baud rate with some margin.  An online path loss calculator at \cite{site-pathLossCalculator} was used to calculate attenuation due to distance, and the Python tool \textit{link budget} was used to calculate atmospheric losses. All values were based on both the RA-02 and the SX1278 chip specifications; dipoles as antennas; an impedance mismatch loss of 0.5 dB (around -10 dB return loss); and a maximum transmitter power setting (18 dBm). The final link budget therefore results in 18.65 dBm - 129.89 dB + 119.65 dBm = 8.41 dB of link margin. Although this is theoretically adequate (above the 3 dB recommendation), there are some additional considerations. Firstly, if a higher bit rate is required (e.g. 38.4 kbps) then the margin drops to -2.6 dB. Secondly, if a longer range is required (e.g. for future projects), free space path loss will drastically increase. For example, for a 250 km range, the loss becomes 133 dB, meaning the margin drops to only 1.1 dB. The system will therefore be designed for a 10 dB link margin. An antenna with at least 2.59 dBi additional gain (i.e. 4.74 dBi gain total) should therefore be designed for the ground station. Then, if necessary, the 20 dB recommendation can be reached by lowering the LoRa spreading factor (SF) to support any ``mission critical" requirements.

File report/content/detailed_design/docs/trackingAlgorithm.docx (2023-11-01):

No

Yes

Move to the pointing location

Is the maximum angle that needs to be moved greater than 5 degrees?

Yes

No

Finish

Update Tracking

Set the active instant to the next path instant while updating the previous path instant to the previous active instant

Set the pointing location to the GPS received location

Yes

Set the pointing location to a time-based linear interpolation between the previous and active path instants

Is the current time older than the next path instant’s time?

Is the latest received GPS co-ordinate less than 60 seconds old?


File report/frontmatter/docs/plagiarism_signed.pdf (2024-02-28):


23905093 G.V.C. Allen | 2023/11/06

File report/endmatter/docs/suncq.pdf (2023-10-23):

## SUNCQ Protocol

### Commands

The following lists all commands from TNC to host and vica-versa. The command reservaons are:
- 0x00 to 0x2F | Host-to-TNC DO commands
- 0x30 to 0x5F | Host-to-TNC SET commands
- 0x60 to 0x7F | Host-to-TNC GET commands
- 0x80 to 0x9F | TNC-to-Host STATUS replies
- 0xA0 to 0xCF | TNC-to-Host DATA replies
- 0xD0 to 0xFE | Reserved
- 0xFF | Invalid
Code | Name | Funcon | Payload | Bytes | Comments
0x00 | RESET | Reset the system | - | 0
0x01 | CALIBRATE | Calibrate the system | - | 0 | Full calibraon e.g. ground staon and all sub-systems
0x02 | RETURN_TO_START | Return the system to its starng state. | - | 0 | The starng state is post-calibraon.
0x03 | RETURN_TO_STOW | Return the system to its stow state. | | | The stow state is pre-calibraon. Typically used before system shutdown
0x30 | SET_TNC_MODE | Enter a TNC mode | See TNC_MODE | 1
0x31 | SET_TRACK_MODE | Set tracking mode | See TRACK_MODE | 1
0x32 | SET_PATH_DATA | Upload flight path data | CSV file. See Flight Path Data. | Any | The payload length is provided as the first 8 bytes.
0x33 | SET_POINT_DIRECTION | Set the direcon that the mount should point at | | | Only applicable when no tracking mode is selected
0x60 | GET_SIGNAL_RSSI | Get RSSI of the signal | - 0
0x61 | GET_LOCATION | Get locaon of the ground staon | Lat;Lng;Alt (f32;f32;f32) | 12
0x80 | TNC_STATUS | Sent by the TNC as an ACK or status alert. | See STATUS_CODE. | 1 Status 0x00 is used as an | “ACK” command.
0x81 | TNC_MESSAGE | Sent by the TNC to communicate a String message to the host. | char[] | Any | A newline character terminates the message
0xA0 | SIGNAL_RSSI | Response to GET_SIGNAL_RSSI | float | 4
0xD0-0xFE | RESERVED | Reserved | | | Reserved for future use
0XFF | INVALID | Invalid | | | For internal use

### Details

TNC_MODE
Value | Descripon
0x00 | Normal mode
0x01 | KISS mode. This mode is exited using the KISS 0xFF command.

TRACK_MODE
The tracking mode is a combinaon flag i.e. mulple bits can be ORed together to specify that the payload must be tracked using mulple methods at once.
Value | Descripon
0x00 | No tracking. Mount can be moved by seng the poinng vector.
0x01 | Use uploaded GPS data
0x02 | Use received GPS data (from payload)
0x04 | Use signal strength, but only for an inial scan
0x08 | Use signal strength, with dynamic conical scanning

STATUS_CODE
The following is a list of status codes that might be sent from the TNC to the host:
Value | Descripon
0x00 | Acknowledge
0x01 | Payload tracking unsuccessful/payload lost

Flight path data
Flight path data can be uploaded in the form of a lile-endian binary stream (i.e. each field should be least significant byte first). The first field is a 2-byte number indicang the number of flight path instances to follow. Then, the fields below should be provided. Such a file can be generated by predicng a flight path at hps://predict.sondehub.org/ , generang a CSV file, and then using the data to generated a binary stream. In the current implementaon, only 200 entries are catered for – if longer flights are needed, then mulple streams should be set from the host intermiently. Time should be in Unix me (seconds since Epoch).
Name | Type
Time | uint64
Latude | float32
Longitude | float32
Altude | float32

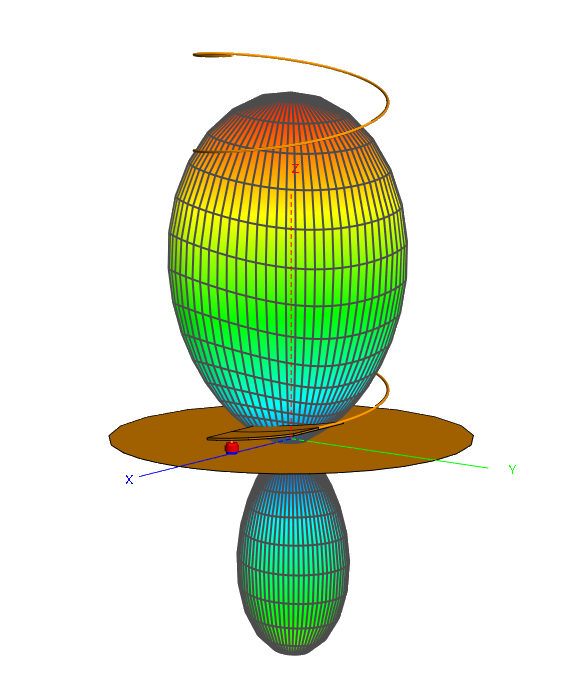
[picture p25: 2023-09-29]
report/content/detailed_design/figures/helix7_pattern_433MHz.png

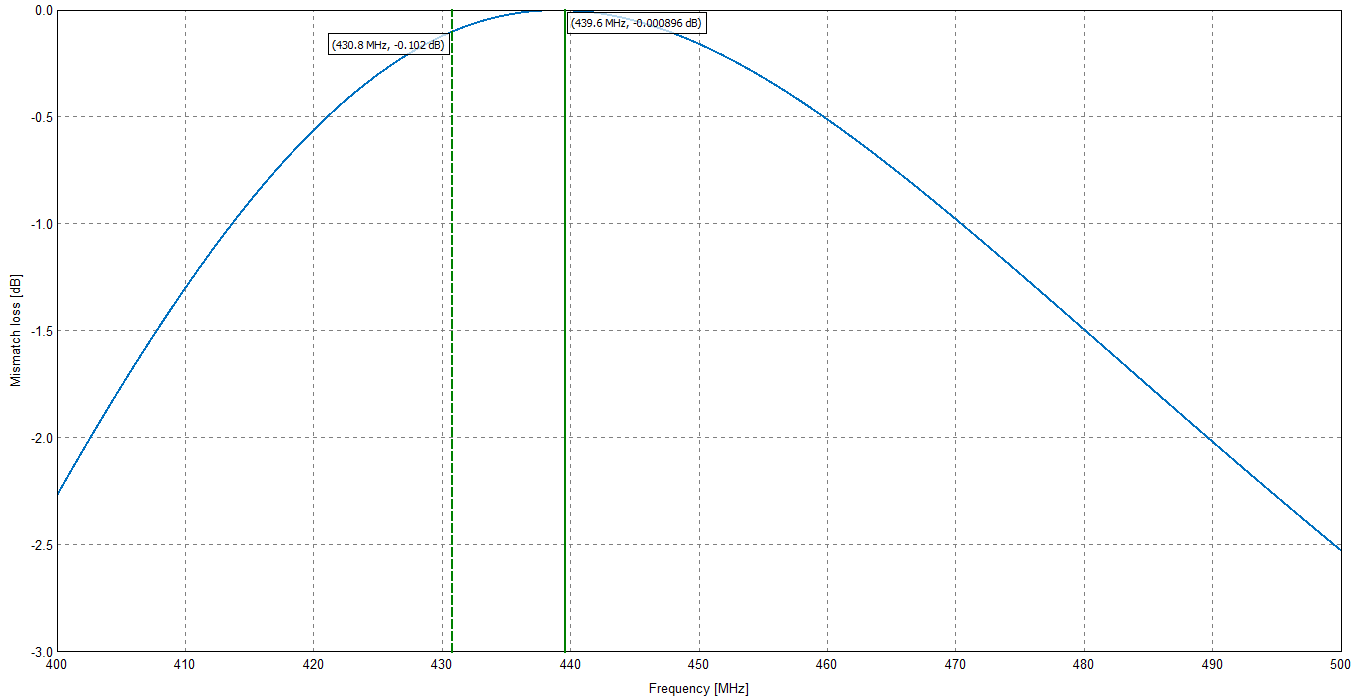
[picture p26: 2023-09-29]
report/content/detailed_design/figures/dipole1_mismatchLoss.png

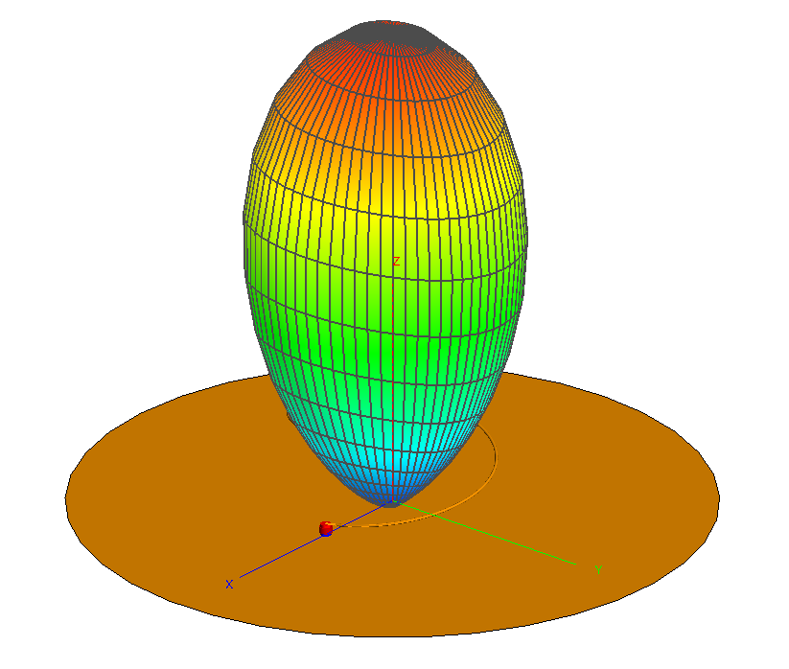
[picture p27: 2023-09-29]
report/content/detailed_design/figures/helix1_pattern_550MHz.png

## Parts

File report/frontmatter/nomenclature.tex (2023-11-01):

% \chapter*{Nomenclature\markboth{}{Nomenclature }}
\chapter*{Nomenclature}
% \addcontentsline{toc}{chapter}{Nomenclature}

% \vspace*{-3mm}
% \subsubsection*{Variables and functions}
% \begingroup
% \renewcommand{\arraystretch}{1.2}
% \renewcommand{\tabularxcolumn}[1]{p{#1}}
% \begin{tabularx}{\textwidth}{@{}p{2.5cm}L}
    % $V$     & Voltage \\
    % $I$     & Current \\
    % $R$     & Resistance \\
% \end{tabularx}
% \endgroup

%\newpage
\subsubsection*{Acronyms and abbreviations}

\begin{tabular}{@{}p{2.5cm} l}
    ACK     & Acknowledge \\
    ASK     & Amplitude Shift Keying \\
    CAD     & Computer-Aided Design \\
    CCSDS   & Consultative Committee for Space Data Systems \\
    CRC     & Cyclic Redundancy Check \\
    CSP     & CubeSat Space Protocol \\
    EIRP    & Equivalent isotropic radiated power \\
    EPS     & Energy Power System \\
    FSK     & Frequency Shift Keying \\
    GFSK    & Gaussian Frequency Shift Keying \\
    GNNS    & Global Navigation Satellite System \\ 
    GPS     & Global Positioning System \\
    GS      & Ground Station \\
    GUI     & Graphical User Application \\
    IC      & Integrated Circuit \\
    IMU     & Inertial Measurement Unit \\
    LEO     & Low Earth Orbit \\
    LOS     & Line-of-Sight \\
    PCB     & Printed Circuit Board \\
    PQ      & PocketQube \\
    PQSU    & PocketQube Stellenbosch University \\
    PEC     & Perfect Electrical Conductor \\
    PSK     & Phase Shift Keying \\
    QAM     & Quadrature Amplitude Modulation \\
    RF      & Radio Frequency \\
    RX      & Receive \\
    SF      & Spreading Factor \\
    SU      & Stellenbosch University \\
    TX      & Transmit \\
\end{tabular}

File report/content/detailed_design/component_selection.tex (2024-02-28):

\graphicspath{{./figures}}

\section{Component Selection}
Components for the various sub-systems should now be selected. Through-hole components and breakout boards will mostly be used for the ground station, and surface mount components for the PQ unit. The existing stepper motors will be used, which draw 0.50 A and allow for up to $\SI{0.5}{N \cdot m}$ of torque \cite{datasheet-4118}. The mount's azimuthal zero-sensing circuit will also be used, which includes a \textit{H22A} optical switch and a low-pass filter.

\subsection{GPS}\label{sec:components_gps}
The same GPS will be selected for both the ground station and PQ unit to simplify development. A one degree pointing accuracy will be designed for, as it is an order of magnitude less than the beamwidth from Section \ref{sec:tracking}. A distance of \SI{120}{km} results in a large required accuracy of $2 \times 120 000 \times \pi \times \frac{1}{360} \approx \SI{2}{km}$. The {ATGM336H} and the \textit{ATGM332D} are two readily available options that advertise 2.5 m accuracy, which is much better than required. Since both of these also have active antenna support, and current consumption less than 100 mA, the ATGM332D-5N31 is chosen for its lower price.

\subsection{IMU}
To automatically determine absolute ground station orientation, the ground station could include an inertial measurement unit (IMU). Alternatively, a \textit{dead-reckoning} fix can be done by ensuring the ground station is flat and manually faced e.g. using a compass and statically stroed magnetic declination value. To provide maximum flexibility in the implementation stage, a 9-axis IMU, which includes both an accelerometer and a magnetometer, will be included. Since the ground station's mount will not be moving, only a low-accuracy accelerometer is assumed to be adequate for orientation. The \textit{MPU-9250} is selected, as it is inexpensive and readily available.

\subsection{RF Module}
The transceiver type for both the custom and radiosonde link needs to be considered. There are a few options in this regard, listed from more to less specialized:
\begin{itemize}
    \item Fully custom design. Here, components are discretely designed using transistors, DSPs etc. This option is listed for completeness, but is out of scope for this project.
    \item Front-End Module (FEM). For this option, the FEM provides filters, a low-noise amplifier (LNA), antenna matching, and down-conversion. Then, a controller (e.g. FPGA or MCU) needs to be designed to perform modulation/demodulation functionality (the \textit{modem}) and interface with the FEM.
    \item Dedicated Transceiver. A transceiver provides FEM and modulation functionality, however still requires RF techniques for matching, and an additional RF shield.
    \item Dedicated module. For this option, all functionality is provided in a dedicated module, with a simple antenna connection or pin-out, and an MCU interface. This method has little flexibility, since all matching and design is done internally, and the frequency band is therefore constrained, however provides high ease-of-use.
    \item Software-defined radio (SDR). This is the most general-purpose option, but does not exercise the highest performance. It is often directly connected to a PC via USB.
\end{itemize}

\subsubsection{Custom Communication}
For the custom link, a dedicated LoRa module will be used. Most of these modules include GFSK as a built-in alternative, making them ideal. All LoRa ICs are based on \textit{Semtech} chipsets due to the company's patent on the technology. Although dedicated transceivers are available, these require special RF considerations to be made, and therefore a module will be utilized to ease development. Table \ref{tab:rfModules} contrasts the two most common modules in the 433 MHz LoRa band. The RA-02 is selected due to availability.

\begin{table}[!htb]
  \centering
  \renewcommand{\arraystretch}{1.2}
  \begin{tabular}{ |c|c|c|c| }
  \hline
  \textbf{Name}   & \textbf{RX Sensitivity} & \textbf{TX Sensitivity}& \textbf{Frequency} \\
  \hline
  RA-02           & -141 dBm             & +18 dBm              & 410 to 525 MHz     \\
  RFM98           & -148 dBm             & +20 dBm              & 410 to 525 MHz     \\
  \hline
  \end{tabular}
  \caption{Comparison of two LoRa modules}
  \label{tab:rfModules}
\end{table}

\subsubsection{Radiosonde Communication}
Unfortunately, although the selected LoRa module supports GFSK demodulation, it does not receive in the meteorological band, and therefore a second receiver is needed for the radiosonde link. To cater for a wide variety of radiosondes, a software-defined radio (SDR) will be used to adjust the decoding parameters dynamically. The \textit{RTL-SDR} USB dongle is considered the standard, low-cost solution for this, and is therefore selected. An alternative option is to design a dedicated GFSK receiver which allows for adjustable parameters, however this route is not chosen due to time constraints.

\subsection{Stepper Motor Driver}
The original PCB of the previous antenna mount contained two A3972 ICs to drive the stepper motors. Although these could be de-soldered and used, it is favourable to use a newer IC for replacement in case of damage. From the driver and motor datasheets, it is realized that the drivers should operate in dual DMOS full-bridge output configuration; allow bipolar PWM current control; allow for micro-stepping; and provide $\SI{0.5}{A}$ at $\SI{24}{V}$. Very few drivers fit these exact specifications. The \textit{A4970} is considered the follow-up version of the \textit{A3972}, however is not available in a single pack or locally. The \textit{L6219} driver is found to match most specifications, while only allowing half-stepping. It is therefore selected, as there is no sound level requirement for the system, and a single step is $0.22^\circ$ and $0.45^\circ$ for the elevation and azimuthal axes respectively, which is fine-grained enough.

\subsection{RS-485 Driver}
An RS-485 driver is needed for compatibility with the PQ bus interface. Due to the project's nature (i.e. all units on the bus are in close proximity) only short-range RS-485 communication should be catered for. Further, the PQSU standard specifies no speed requirements, and therefore a minimum of 9600 baud will be designed for. The \textit{MAX485} is selected both due to its availability, and the fact that it meets these specifications.

\subsection{Microcontroller}
An MCU will be needed both on the GS and the PQ. The ESP32, Arduino, and STM32 frameworks are considered. The \textit{ESP32-WROOM-32} is a commonly available ESP32 variant which has 32 GPIO pins. It also has several ADCs, and allows for both WiFi and Bluetooth connectivity. The \textit{ATMEGA328PB} is an MCU commonly used in small Arduino boards. It has fewer pins than the ESP, is an 8-bit MCU, and has only 32 KB of flash memory, but allows a supply voltage of as low as 1.8 V, and has very low current consumption. Finally, the common \textit{STM32F411} MCU is a high-performance Arm-based MCU, advertised to have highly accurate ADCs and up to 81 GPIOs. Since the processing requirements for this project are assumed to not be high, and the ESP32 is a relatively high-performance MCU which satisfies the pin requirements, it will be selected for the GS. For the PQ unit, the ATMEGA328PB will be used, due to its exceptionally low current consumption, and many fewer pins being needed for the PQ unit.

\subsection{Power}
Both the ground station and the PocketQube should cater for the three-hour flight time. Component power calculations are listed in Tables \ref{tab:gs_component_consumption} and \ref{tab:pqunit_component_consumption}, resulting in 50 W and 453 mW for the GS and PQ respectively. A 12 V lead-acid battery will be used for the ground station. This should be capable of supplying around 4 A, resulting in a capacity requirement of 12 Ah. A more readily available 7.2 Ah battery will initially be used for development. Linear regulators will be used for the 3.3 V and 5 V supply (as opposed to switched-mode) due to their simplicity and the lack of any system-wide efficiency specifications. The 3.3 V regulator should be capable of supplying 130 mA to the RF module, GPS, and IMU, and the 5 V regulator should be capable of supplying $\SI{120}{mA} + \SI{130}{mA} = \SI{250}{mA}$ to the ESP and 3.3 V regulator. The LD1117CV and L7805CP are linear regulators which can supply up to $\SI{800}{mA}$ and $\SI{1.5}{A}$ respectively, and therefore meet these requirements. A boost converter will be used to achieve the 24 V motor drive voltage, which should support \SI{2}{A} at its \SI{12}{V} input due to the motors drawing 0.5 A per coil. A breakout board based on the XL6009 IC will be used, which meets this requirement. For the PocketQube unit, the LiPo battery should be capable of supplying around 120 mA nominally. To achieve the 3 hour specification, a capacity of 360 mAh is required. A larger 2000 mAh battery will be used for development, due to its low-cost; the added convenience of fewer discharge cycles; as well as the allowance it provides for retrieving the payload after the balloon has landed at the end of the day (around 16 hours later).

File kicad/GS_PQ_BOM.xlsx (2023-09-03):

# | Reference | Qty | Value | Footprint | Added
1 | C1 | 1 | 1uF | Capacitor_SMD:C_1206_3216Metric_Pad1.33x1.80mm_HandSolder | Y
2 | C2 | 1 | 4.7uF | Capacitor_SMD:C_1206_3216Metric_Pad1.33x1.80mm_HandSolder | YY
3 | C4, C5, C8, C9 | 4 | 100nF | Capacitor_SMD:C_0805_2012Metric_Pad1.18x1.45mm_HandSolder | Y
4 | C10 | 1 | 22uF | Capacitor_SMD:C_1206_3216Metric_Pad1.33x1.80mm_HandSolder
1 | C1 | 1 | 0.33uF | Capacitor_THT:C_Rect_L7.0mm_W4.5mm_P5.00mm
2 | C2 | 1 | 0.1uF | Capacitor_THT:C_Rect_L7.0mm_W4.5mm_P5.00mm
3 | C3 | 1 | 10uF | Capacitor_THT:C_Rect_L7.0mm_W4.5mm_P5.00mm
4 | C4, C5, C7, C8, C14, C15, C21 | 7 | 100nF | Capacitor_THT:C_Rect_L7.0mm_W4.5mm_P5.00mm
5 | C6 | 1 | 22uF | Capacitor_THT:CP_Radial_D5.0mm_P2.00mm
6 | C9, C16 | 2 | 100uF | Capacitor_THT:CP_Radial_D5.0mm_P2.00mm
7 | C10, C11, C12, C13, C17, C18, C19, C20 | 8 | 820pF | Capacitor_THT:C_Rect_L4.6mm_W2.0mm_P2.50mm_MKS02_FKP02
20 | R6, R8, R12, R14 | 4 | 1Ω1W | Resistor_THT:R_Axial_DIN0207_L6.3mm_D2.5mm_P10.16mm_Horizontal | Y
14 | JP1 | 4 | PowerSelect_3V3 | Connector_PinHeader_2.54mm:PinHeader_1x02_P2.54mm_Vertical | Y
11 | J4 | 1 | Conn_02x10_Odd_Even | Connector_PinHeader_2.54mm:PinHeader_2x10_P2.54mm_Vertical | Y
12 | J5 | 1 | PowerBreakout | Connector_PinHeader_2.54mm:PinHeader_1x05_P2.54mm_Vertical | Y
5 | J1 | 1 | Conn_02x10_PQSU | Connector_PinSocket_2.54mm:PinSocket_2x10_P2.54mm_Vertical | Y
6 | J2 | 1 | Conn_01x10 | Connector_PinSocket_2.54mm:PinSocket_1x10_P2.54mm_Vertical | Y
9 | J2 | 1 | JST_MotorAz | Connector_JST:JST_PH_B4B-PH-K_1x04_P2.00mm_Vertical
10 | J3 | 1 | JST_MotorEl | Connector_JST:JST_PH_B4B-PH-K_1x04_P2.00mm_Vertical
13 | J6 | 1 | JST_ZeroAZ | Connector_JST:JST_PH_B5B-PH-K_1x05_P2.00mm_Vertical
8 | U1 | 1 | ATMEGA328P-AU | Package_QFP:TQFP-32_7x7mm_P0.8mm | Y
9 | U5 | 1 | MAX485E | MAX485:SO08 | Y
10 | U6 | 1 | Ai-Thinker-Ra-02 | RF_Module:Ai-Thinker-Ra-01-LoRa | Y
11 | Y1 | 1 | Crystal | Crystal:Crystal_SMD_HC49-SD | Y
 |  |  |  | Battery | Y
 |  |  |  | Battery charger | Y

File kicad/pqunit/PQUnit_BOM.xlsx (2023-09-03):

# | Reference | Qty | Value | Footprint | DNP
1 | C1 | 1 | 1uF | Capacitor_SMD:C_0805_2012Metric_Pad1.18x1.45mm_HandSolder
2 | C2 | 1 | 4.7uF | Capacitor_SMD:C_1206_3216Metric_Pad1.33x1.80mm_HandSolder
3 | C4, C5, C8, C9 | 4 | 100nF | Capacitor_SMD:C_0603_1608Metric_Pad1.08x0.95mm_HandSolder
4 | C10 | 1 | 22uF | Capacitor_SMD:C_0805_2012Metric_Pad1.18x1.45mm_HandSolder
5 | J1 | 1 | Conn_02x10_PQSU | Connector_PinSocket_2.54mm:PinSocket_2x10_P2.54mm_Vertical
6 | J2 | 1 | Conn_01x10 | Connector_PinSocket_2.54mm:PinSocket_1x10_P2.54mm_Vertical
7 | R3, R4 | 2 | 1.2k | Resistor_SMD:R_0805_2012Metric_Pad1.20x1.40mm_HandSolder
8 | U1 | 1 | ATMEGA328P-AU | Package_QFP:TQFP-32_7x7mm_P0.8mm
9 | U5 | 1 | MAX485E | MAX485:SO08
10 | U6 | 1 | Ai-Thinker-Ra-02 | RF_Module:Ai-Thinker-Ra-01-LoRa
11 | Y1 | 1 | Crystal | Crystal:Crystal_SMD_HC49-SD
# | Reference | Qty | Value | Footprint | DNP
1 | C1 | 1 | 0.33uF | Capacitor_THT:C_Rect_L7.0mm_W4.5mm_P5.00mm
2 | C2 | 1 | 0.1uF | Capacitor_THT:C_Rect_L7.0mm_W4.5mm_P5.00mm
3 | C3 | 1 | 10uF | Capacitor_THT:C_Rect_L7.0mm_W4.5mm_P5.00mm
4 | C4, C5, C7, C8, C14, C15, C21 | 7 | 100nF | Capacitor_THT:C_Rect_L7.0mm_W4.5mm_P5.00mm
5 | C6 | 1 | 22uF | Capacitor_THT:CP_Radial_D5.0mm_P2.00mm
6 | C9, C16 | 2 | 100uF | Capacitor_THT:CP_Radial_D5.0mm_P2.00mm
7 | C10, C11, C12, C13, C17, C18, C19, C20 | 8 | 820pF | Capacitor_THT:C_Rect_L4.6mm_W2.0mm_P2.50mm_MKS02_FKP02
8 | J1 | 1 | Jack_12V | Connector_BarrelJack:BarrelJack_Kycon_KLDX-0202-xC_Horizontal
9 | J2 | 1 | JST_MotorAz | Connector_JST:JST_PH_B4B-PH-K_1x04_P2.00mm_Vertical
10 | J3 | 1 | JST_MotorEl | Connector_JST:JST_PH_B4B-PH-K_1x04_P2.00mm_Vertical
11 | J4 | 1 | Conn_02x10_Odd_Even | Connector_PinHeader_2.54mm:PinHeader_2x10_P2.54mm_Vertical
12 | J5 | 1 | PowerBreakout | Connector_PinHeader_2.54mm:PinHeader_1x05_P2.54mm_Vertical
13 | J6 | 1 | JST_ZeroAZ | Connector_JST:JST_PH_B5B-PH-K_1x05_P2.00mm_Vertical
14 | JP1 | 1 | PowerSelect_3V3 | Connector_PinHeader_2.54mm:PinHeader_1x02_P2.54mm_Vertical
15 | JP2 | 1 | PowerSelect_5V | Connector_PinHeader_2.54mm:PinHeader_1x02_P2.54mm_Vertical
16 | JP3 | 1 | PowerSelect_24V | Connector_PinHeader_2.54mm:PinHeader_1x02_P2.54mm_Vertical
17 | R1, R5, R7, R11, R13 | 5 | 1k | Resistor_THT:R_Axial_DIN0207_L6.3mm_D2.5mm_P10.16mm_Horizontal
18 | R2 | 1 | 20k | Resistor_THT:R_Axial_DIN0207_L6.3mm_D2.5mm_P10.16mm_Horizontal
19 | R3, R4, R9, R10 | 4 | 56k | Resistor_THT:R_Axial_DIN0207_L6.3mm_D2.5mm_P10.16mm_Horizontal
20 | R6, R8, R12, R14 | 4 | 1Ω | Resistor_THT:R_Axial_DIN0207_L6.3mm_D2.5mm_P10.16mm_Horizontal
21 | R15 | 1 | 10k | Resistor_THT:R_Axial_DIN0207_L6.3mm_D2.5mm_P10.16mm_Horizontal
22 | U1 | 1 | ESP32-WROOM-32-DEV | ESP32-WROOM-32PCB:ESP32-WROOM-32PCB
23 | U2 | 1 | MPU-9250-DEV | MPU-9250-PCB:MPU-9250-PCB
24 | U3 | 1 | Ai-Thinker-Ra-02 | RA-02-PCB:RA-02-PCB
25 | U4 | 1 | L7805 | Package_TO_SOT_THT:TO-220-3_Horizontal_TabDown
26 | U5 | 1 | LD1117S33TR_SOT223 | Package_TO_SOT_THT:TO-220-3_Horizontal_TabDown
27 | U6, U8 | 2 | L6219DS | L6219DS:SOIC127P1030X265-24N
28 | U7 | 1 | ~ | XL6009PCB:XL6009PCB
29 | U9 | 1 | ATGM332D-5N31-PCB | ATGM332D-5N31-PCB:ATGM332D-5N31-PCB

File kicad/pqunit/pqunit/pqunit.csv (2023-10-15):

# | Reference | Qty | Value | Footprint | DNP
1 | C1 | 1 | 1uF | Capacitor_SMD:C_1206_3216Metric_Pad1.33x1.80mm_HandSolder
2 | C2 | 1 | 4.7uF | Capacitor_SMD:C_1206_3216Metric_Pad1.33x1.80mm_HandSolder
3 | C4, C5, C8, C9 | 4 | 100nF | Capacitor_SMD:C_0805_2012Metric_Pad1.18x1.45mm_HandSolder
4 | C6 | 1 | 10uF | Capacitor_SMD:C_1206_3216Metric_Pad1.33x1.80mm_HandSolder
5 | C10 | 1 | 22uF | Capacitor_SMD:C_1206_3216Metric_Pad1.33x1.80mm_HandSolder
6 | J1 | 1 | Conn_02x10_PQSU | Connector_PinSocket_2.54mm:PinSocket_2x10_P2.54mm_Vertical
7 | J2 | 1 | Conn_01x10 | Connector_PinSocket_2.54mm:PinSocket_1x10_P2.54mm_Vertical
8 | J3 | 1 | Conn_Coaxial | Connector_Coaxial:U.FL_Molex_MCRF_73412-0110_Vertical
9 | R3, R4 | 2 | 1.2k | Resistor_SMD:R_0805_2012Metric_Pad1.20x1.40mm_HandSolder
10 | U1 | 1 | ATMEGA328P-AU | Package_QFP:TQFP-32_7x7mm_P0.8mm
11 | U2 | 1 | Ai-Thinker-Ra-02 | RF_Module:Ai-Thinker-Ra-01-LoRa
12 | U3 | 1 | ATGM332D-5N31 | LIB_ATGM332D-5N31:ATGM332D5N31
13 | U4 | 1 | MAX485E | MAX485:SO08
14 | Y1 | 1 | Crystal | Crystal:Crystal_SMD_HC49-SD

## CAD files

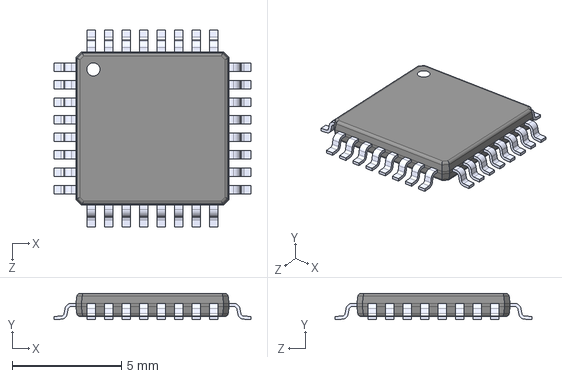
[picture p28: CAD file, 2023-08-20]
kicad/components/ATMEGA328P-AU/ATMEGA328P-AU.step
9.00 x 1.20 x 9.00 mm

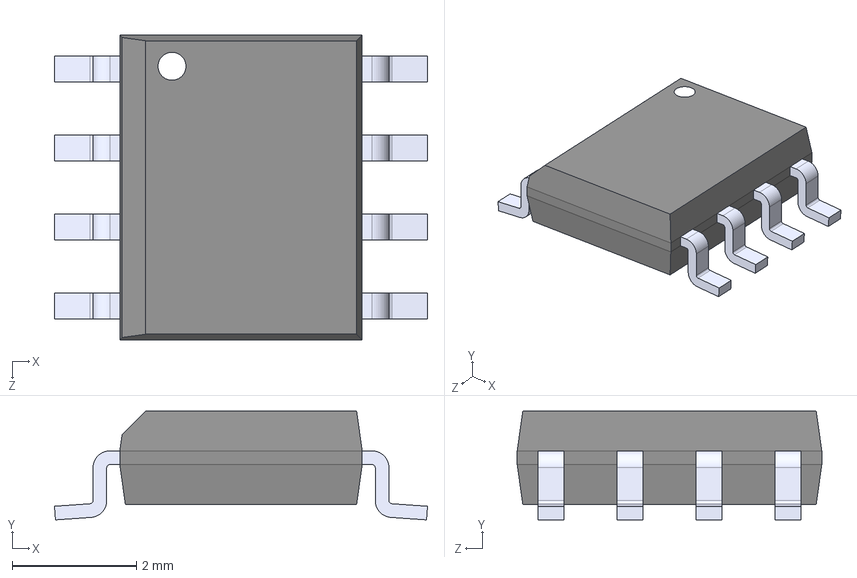
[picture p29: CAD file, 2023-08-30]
kicad/components/MAX485/MAX485.step
6.00 x 1.75 x 4.90 mm

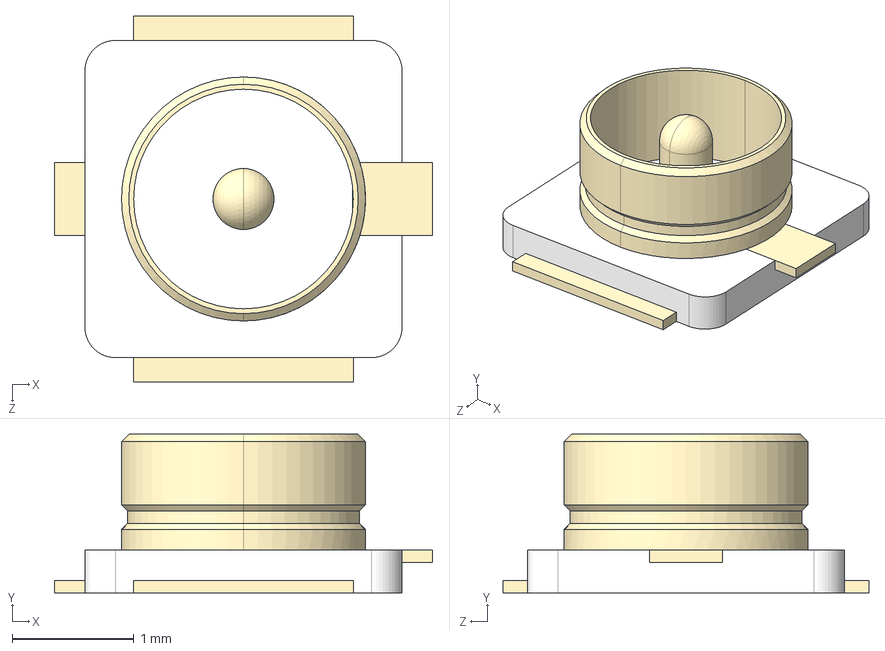
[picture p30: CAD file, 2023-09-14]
kicad/components/UFL/CONUFL001-SMD.step
3.10 x 1.30 x 3.00 mm

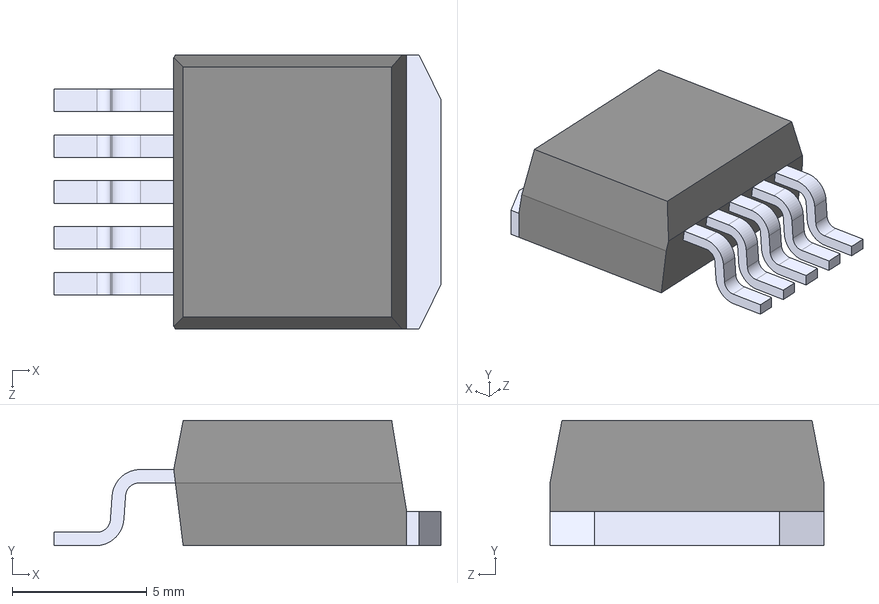
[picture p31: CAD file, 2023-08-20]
kicad/components/XL6009/XL6009.step
14.3 x 4.65 x 10.2 mm

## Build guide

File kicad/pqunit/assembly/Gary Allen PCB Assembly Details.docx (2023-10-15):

# Gary Allen PCB Assembly Details

# | Reference | Qty | Value | Footprint

1 | C4, C5, C8, C9 | 4 | 100nF | Capacitor_SMD:C_0805_2012Metric_Pad1.18x1.45mm_HandSolder
2 | C1 | 1 | 1uF | Capacitor_SMD:C_1206_3216Metric_Pad1.33x1.80mm_HandSolder
3 | C2 | 1 | 4.7uF | Capacitor_SMD:C_1206_3216Metric_Pad1.33x1.80mm_HandSolder
5 | C6, C10 | 1 | 22uF | Capacitor_SMD:C_1206_3216Metric_Pad1.33x1.80mm_HandSolder
9 | R3, R4 | 2 | 1.2k | Resistor_SMD:R_0805_2012Metric_Pad1.20x1.40mm_HandSolder
10 | U1 | 1 | ATMEGA328P-AU | Package_QFP:TQFP-32_7x7mm_P0.8mm
11 | U2 | 1 | Ai-Thinker-Ra-02 | RF_Module:Ai-Thinker-Ra-01-LoRa
13 | U4 | 1 | MAX485E | MAX485:SO08
14 | Y1 | 1 | Crystal | Crystal:Crystal_SMD_HC49-SD

Reference | Pin #1 on IC | Pin #1 on PCB
U1 | Marked | Bottom right
U2 | Next to Molex connector | Top left
U4 | Marked | Marked

(“Bottom right” etc. is relative to when the text is placed upright on that side of the board)

Capacitor Value | Package | Size
100nF | White reel of 10 | 0805
1uF | Transparent reel of 2 | 1206
4.7uF | White reel of 2 | 1206
22uF | Transparent reel of 10 | 1206

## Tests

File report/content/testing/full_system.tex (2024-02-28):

\graphicspath{{./figures}}

\section{Full System}

The South African Weather Service kindly granted permission to track their weather balloons, which have radiosonde payloads. This allowed for full system tests to be conducted, with focus on closed-loop tracking. A first test was conducted near the launch location (Cape Town International Airport), where closed-loop tracking was tested. Although the system computer unfortunately lost power near the 25 km mark, it was observed that the mount correctly steered the antenna based on the received GPS data. The results of both the predicted path and the actual path for this test, as well as the recorded SNR as a function of distance, are shown in Figures \ref{fig:radiosondePredictedVsActual} and \ref{fig:radiosondeSnr}. A second test was conducted from Constantia, around 17 km from launch. The mount correctly pointed towards the launch location using an open-loop uploaded path. Then, at an altitude of $\SI{5.1}{km}$, the system successfully received the radiosonde's GPS location. Unfortunately, due to time constraints, the test was then concluded.

\begin{figure}[!htb]
  \begin{minipage}{.4\textwidth}
    \centering
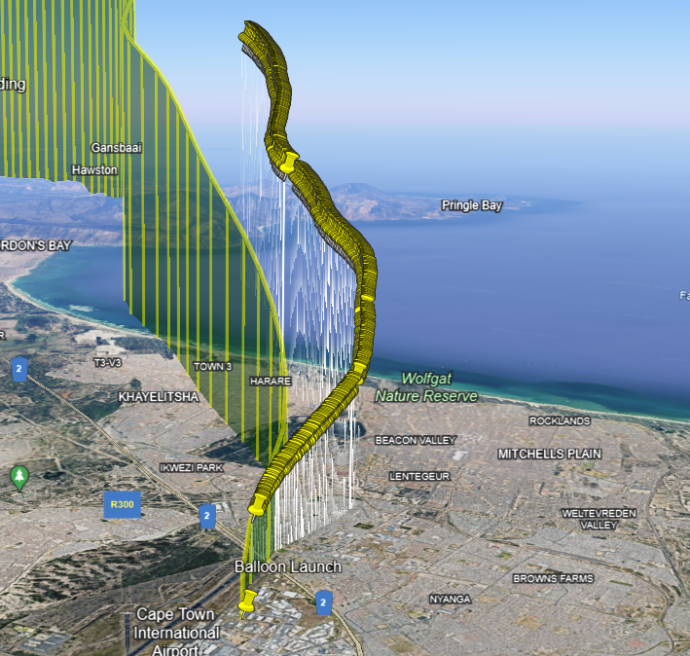
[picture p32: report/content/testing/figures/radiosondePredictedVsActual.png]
    
    \caption{Radiosonde Closed-Loop Tracking Predicted Path (left) vs Actual (right)}
    \label{fig:radiosondePredictedVsActual}
  \end{minipage}
  \begin{minipage}{.6\textwidth}
    \centering
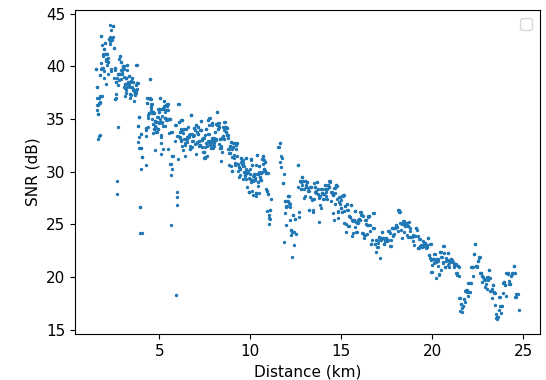
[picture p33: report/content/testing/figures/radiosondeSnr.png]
    
    \caption{Radiosonde Closed-Loop Tracking SNR vs Distance}
    \label{fig:radiosondeSnr}
  \end{minipage}
\end{figure}

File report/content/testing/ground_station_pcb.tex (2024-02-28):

\section{Ground Station PCB}

After implementation, initial tests were done to ensure the ground station was functional. This included ensuring all modules (radio, GPS and IMU) could be interfaced with successfully, as well as a few more detailed power tests, documented below.

\subsection{Power}

During no load from the motors, the voltage readings in Table \ref{tab:gs_pcb_voltage} were obtained. The ESP and GPS lights were noted to be on. From these tests, it is clear that the full power system is working as expected. The current through a 12.3 V supply was measured at 179 mA i.e. 2.2 W power. Since a total of around 1 W of power is expected during no transmission (see Table \ref{tab:gs_component_consumption}), this means that the voltage regulators are dissipating the remaining 1.2 W. This is well within the limitations of both regulators e.g. the LD1117 can dissipate a theoretical maximum of $\SI{12}{W}$. The system was then left idle for an hour, with no noticeable change in current or heat.
\begin{table}[!htb]
  \centering
  \renewcommand{\arraystretch}{1.2}
  \begin{tabular}{ |c|c|c| }
  \hline
  \textbf{Component}        & \textbf{Expected}     & \textbf{Measured}  \\
  \hline
  LD1117                 &  3.3 V             & 3.307 V \\  \hline
  LM7805                 &  5 V               & 5.069 V \\  \hline
  XL6009                 &  24 V             & 24.07 V  \\ \hline
  \end{tabular}
  \caption{Ground Station Voltage Measurements}
  \label{tab:gs_pcb_voltage}
\end{table}

\subsection{Motor Drive}
The motor drive system was tested with the half-step sequence mentioned. Current measurements were made for different operating conditions and are listed in Table \ref{tab:motorDriveTests}. Tests 1-4 were conducted using a \textit{calibrate - return to stow} cycle repeated 10 times at 2/3 maximum current. The goal of these tests was to determine the speed limitations of the system, since it is easy to identify if the system misses steps, or if the gears slip, by moving it back and forth continuously. Tests 5-6 were conducted with the mount stationary at 75 degrees elevation with 2/3 and 3/3 current, respectively. These tests were intended to stress test the current handling and heat dissipation capabilities of the system. Note that the idle current of 179 mA was subtracted from each measurement.

\begin{table}[!htb]
  \centering
  \renewcommand{\arraystretch}{1.2}
  \begin{tabular}{ |p{0.8cm}|c|c|c| }
  \hline
  \textbf{Test No.}  & \textbf{Description} & \textbf{$I_{\textbf{avg}}$ (A)} & \textbf{Observation} \\
  \hline
  1
  & $\SI{40}{ms}$ step delay           
  & 0.7
  & No noticeable steps missed
  \\  \hline
  2
  & $\SI{20}{ms}$ step delay           
  & 0.7
  & No noticeable steps missed
  \\  \hline
  3
  & $\SI{10}{ms}$ step delay           
  & 0.56
  & Small slip near calibration start
  \\  \hline
  4
  & $\SI{5}{ms}$ step delay           
  & 0.25
  & Large number of steps missed
  \\  \hline
  5
  & 2/3 current; 1 hour
  & 0.71
  & Minimal system change across the hour
  \\  \hline
  6
  & 3/3 current; 1 hour
  & 2.1
  & Stabilised current but very hot mount
  \\  \hline
  \end{tabular}
  \caption{Motor Drive Operating Tests @ 12 V supply}
  \label{tab:motorDriveTests}
\end{table}

Since the boost converter operates as a DC transformer, the current consumed by the motor drive near the start of the hour can be calculated as $2.031 \times \frac{12}{24} \div 2 = \SI{0.509}{A}$. This is slightly higher than the designed reference current of 475 mA, however it is assumed that the L6219 was dissipating the remainding power, since it was indeed observed to increase in temperature. Since the system is stable near the end of the hour, and the L6219 has thermal shutdown, the system is considered to be within a safe operating region. Lastly, it should be noted that, although the stepper motors meet the torque requirements, it is clear that the mount's gear system was not designed for such a large load. Future projects should therefore consider a stronger design.

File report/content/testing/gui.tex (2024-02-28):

\graphicspath{{./figures}}

\section{GUI}

The interface was tested to ensure that it met the desired functionality. An example of the output received on the GUI's monitor is shown in Figure \ref{fig:guiOpenLoop}, after the calibration button was pressed; flight path data was uploaded; the tracking method was set to open-loop (``GPS Uploaded"); and the system was left for some time. Further outputs, as well as the whole interface, are shown in Appendix \ref{sec:appendix_gui}.

\begin{figure}[!htb]
  \centering
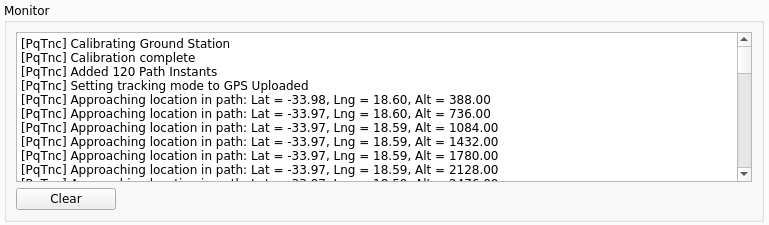
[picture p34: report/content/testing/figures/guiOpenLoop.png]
  
  \caption{GUI Monitor after \textit{``Calibrate''}, \textit{``Upload''}, and \textit{``Set Track Mode''}}
  \label{fig:guiOpenLoop}
\end{figure}

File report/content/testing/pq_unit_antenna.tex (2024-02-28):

\graphicspath{{./figures}}

\section{PocketQube Unit Antenna}

The return loss of the dipole antenna is shown in Figure \ref{fig:dipoleReturnLoss}. It is clear that the resulting match is successful. Since frequencies from 420 to 440 MHz provide less than 0.1 dB mismatch loss, a final system frequency of around $\SI{430}{MHz}$ can be selected, chosen solely based on the helical antenna's return loss.

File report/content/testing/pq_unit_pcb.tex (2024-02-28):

\section{PocketQube Unit PCB}

As mentioned, it was decided that a balloon satellite would not be flown by the E\&E department. Therefore, integration with the other PocketQube modules was not prioritised for the PCB and the RS-485 line drivers were not soldered onto the board. Current consumption for the rest of the components, however, was measured at 31 mA when the system was directly powered from a power supply running at 3.3 V. This is only 6 mA lower than the total current expected from the GPS and MCU ICs, indicating conformance to the original design.

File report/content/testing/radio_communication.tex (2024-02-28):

\graphicspath{{./figures}}

\section{RF Module}

\subsection{Initial Tests}
The radio modules were initially tested using two small, 433 MHz helical antennas. The first was placed near a window indoors, and the second inside a car. A range of 50 m was recorded in an urban area with a LoRa spreading factor of 8. This test served merely as a ``proof-of-concept", and was not intended as an indication of system performance.

\subsection{Transmit Power Consumption}
The custom-built antennas were then connected to both the PQ and the GS and more detailed tests were conducted. The first test measured the power consumption for the PQ unit as a function of transmit power. This is displayed in Figure \ref{fig:txPower}, after subtracting a 31 mA ``no-transmit" current. The maximum current is around 96 mA for the maxium output power (quoted by the RA-02 as 18 dBm +- 1 dBm).

\subsection{Data Rate}
To test the possible bit rates as a function of LoRa spreading factor (SF), two RA-02 modules were setup with the same parameters and the bit rate was measured as the SF value was varied. A payload length of 255 was used, with 4/6 CRC, an 8 bit preamble, 500 kHz bandwidth, and a 10 ms delay between packets. The bit rate was then measured on the receiving side and compared to theoretical bit rates derived using the calculator at \cite{site-loraBitRateCalculator} (as shown in Table \ref{tab:loraBitRate}). The results show that the system is set up correctly, and that a spreading factor of 8 is the correct choice to achieve the 9600 baud rate requirement.

\begin{figure}[!htb]
  \begin{minipage}{.49\textwidth}
    \centering
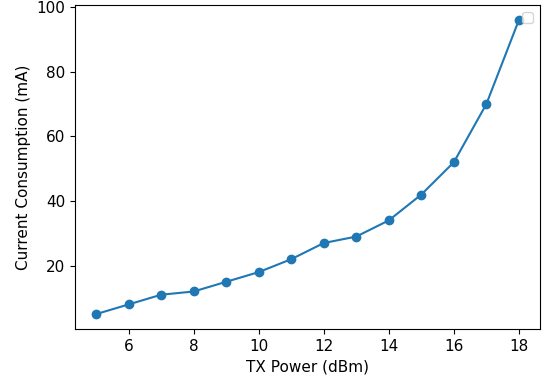
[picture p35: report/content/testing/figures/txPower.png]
    
    \caption{TX Output Power vs Current Consumption}
    \label{fig:txPower}
  \end{minipage}
  \begin{minipage}{.49\textwidth}
      \centering
      \renewcommand{\arraystretch}{1.2}
      \begin{tabular}{ |p{2cm}|p{2.5cm}|p{2.5cm}| }
        \hline
        \textbf{Spreading Factor}        & \textbf{Theoretical Bit Rate (bps)}      & \textbf{Measured Bit Rate (bps)}    \\
        \hline
        7         & 18229         & 17200       \\  \hline
        8         & 10417         & 10240       \\  \hline
        9         & 5859          & 5800        \\  \hline
        10        & 3255          & 3320        \\  \hline
        11        & 1790          & 1846        \\  \hline
      \end{tabular}
      \caption{LoRa Bit Rate vs Spreading Factor}
      \label{tab:loraBitRate}
  \end{minipage}
  
\end{figure}

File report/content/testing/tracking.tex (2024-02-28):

\graphicspath{{./figures}}

\section{Tracking and Pointing}

\subsection{Open-Loop}

In order to test the GPS pointing and open-loop tracking, a map was printed with lines pointing to nearby locations from a pre-determined location. The ground station was then placed on top of this map at this location and calibrated (as described in Appendix \ref{sec:appendix_mount_calibration}). This test had multiple goals i.e. to test the mount transfer function, the GPS co-ordinate pointing, and the flight path tracking. An image of the test setup is shown in Figure \ref{fig:pointingTestSetup}.

Flight path data containing the map locations was then uploaded, and the azimuthal angle was qualitatively confirmed to point in the map directions using a ruler. The elevation angle was measured using a protractor and found to be within $5^\circ$ of the expected angle. The system was also found to successfully point towards the commanded locations at the desired times. Since the beamwidth of the antenna is on the order of $70^\circ$, it was decided not to use a more accurate testing technique, since it is clear the system was functional at least within requirements.

\subsection{Closed-Loop}\label{sec:closed_loop_testing}
\begin{figure}[!tb]
  \begin{minipage}{.49\textwidth}
    \centering
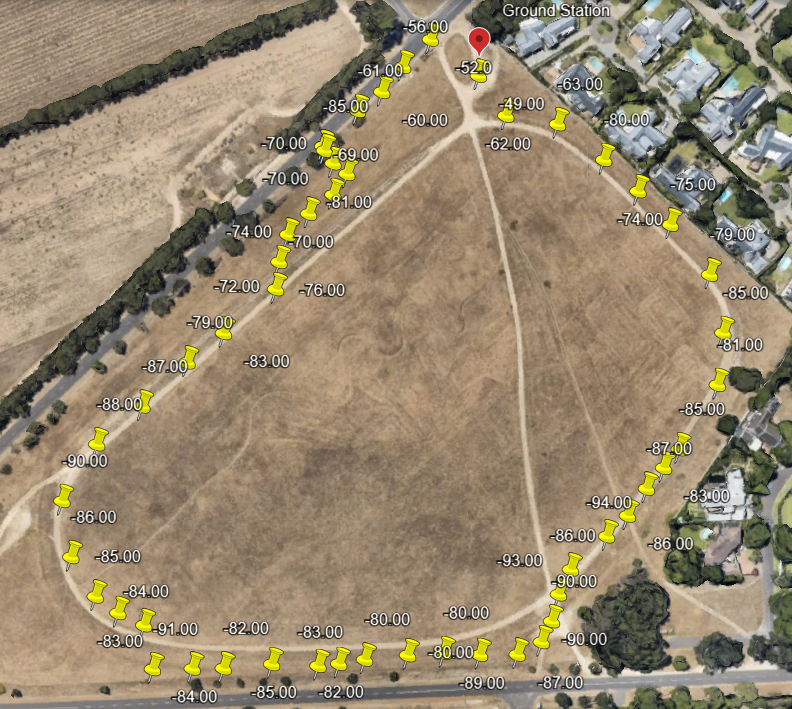
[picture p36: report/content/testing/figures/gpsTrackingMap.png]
    
    \caption{GPS Tracking Locations and RSSI Values}
    \label{fig:gpsTrackingMap}
  \end{minipage}
  \begin{minipage}{.49\textwidth}
    \centering
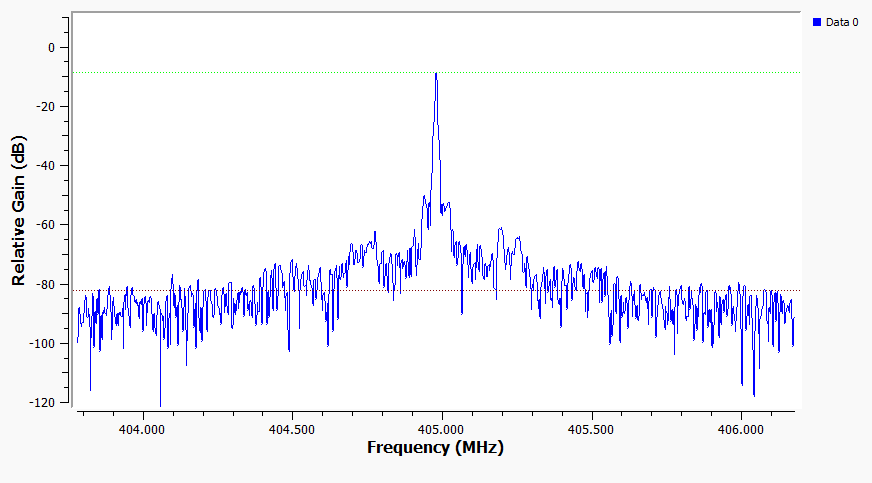
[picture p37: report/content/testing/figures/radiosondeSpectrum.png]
    
    \caption{Received Radiosonde Signal Spectrum}
    \label{fig:radiosondeSpectrum}
  \end{minipage}
\end{figure}

Closed-loop GPS tracking was tested on an open field at \SI{300}{m} range. The PQ unit was carried around the field at a walking speed of $\SI{2}{m.s^{-1}}$ while transmitting its GPS location. Both the RSSI, and the antenna pointing direction, were recorded. The system was observed to successfully track the transmitter around the field without noticeable delay. The $90^\circ$ turn created by the furthest ends of the field creates an approximate 500 m path, which was covered in 100 s. This results in a turning rate of around $0.9 ^ \circ$, which meets the requirement of $0.015 ^ \circ$. The tracking was observed to be successful until the target reached a distance of around 10 m, where the pointing direction became unpredictable. This is attributed to the low accuracy of the GPS modules.

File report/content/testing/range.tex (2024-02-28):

\graphicspath{{./figures}}

\section{Range}

Line-of-sight range tests were conducted. Both antennas were manually positioned, and the PQ dipole was placed both horizontally and vertically. All measurements were done at the designed parameters i.e. SF 8, CR 4/6 and 500 kHz. The resulting \textit{received signal strength indicator} (RSSI) and signal-to-noise (SNR) ratio was recorded. For the unfamiliar reader, the best theoretical RSSI is 0 dB, and the minimum SNR for SF 8 is -10 dB.

Tests were done in locations around the Western Cape up until $\SI{122}{km}$, as described in Appendx \ref{sec:appendix_range}. The first test (not listed) was a 300 m test on Coetzenburg field in Stellenbosch. The link performance was found to be low compared to subsequent tests, with a recorded RSSI of -92 dBm. It is assumed that ground bounce was the major contributing factor.

\begin{figure}[!htb]
  \begin{minipage}{0.49\textwidth}
    \centering
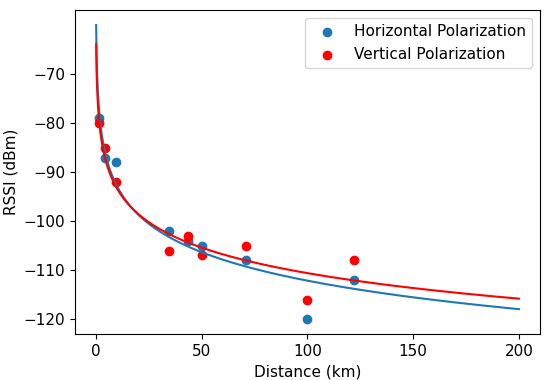
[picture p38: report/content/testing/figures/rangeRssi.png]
    
    \caption{Measured RSSI vs Distance}
    \label{fig:rangeRssi}
  \end{minipage}
  \begin{minipage}{0.49\textwidth}
    \centering
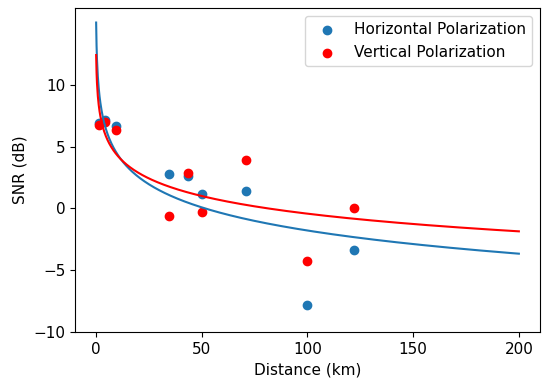
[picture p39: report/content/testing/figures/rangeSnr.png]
    
    \caption{Measured SNR vs Distance}
    \label{fig:rangeSnr}
  \end{minipage}
\end{figure}

The results for the rest of the tests are plotted in Figures \ref{fig:rangeRssi} and \ref{fig:rangeSnr}, with a logarithmic curve fit. The packet contents were verified using an ID, the transmitted GPS location, and by inspecting whether a CRC (Cyclic Redundancy Check) error had occurred. The system successfully met the 120 km range requirement, and a reliable link was established at the final test of 122 km, with a recorded RSSI of -108 dBm for the vertically polarized case. Although the SNR appears to be adjusted by the receiver at closer distances, the RSSI appears to follow a logarithmic curve well, as predicted by the free space path loss formula. All tests also achieved a 100\% packet reception rate once in steady-state. For the required distance, at a sensitivity of -119 dBm, this indicates an 11 dB margin, which is slightly less than the final designed value of 12.8 dB. It is clear that the 100 km is an outlier, and it is assumed that this was due to strong multi-pathing effects caused by the transmitter being sub-optimally placed, with a large rock directly behind it.

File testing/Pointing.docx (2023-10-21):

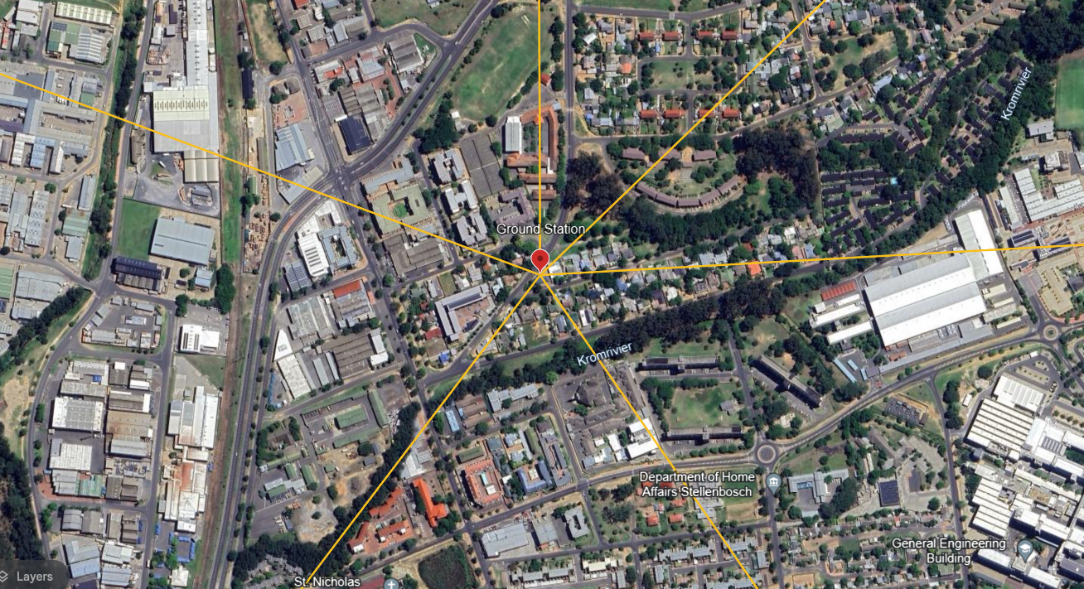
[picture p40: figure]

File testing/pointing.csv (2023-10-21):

datetime | latitude | longitude | altitude
2023-10-19T10:00:00Z | -33.86722044711264 | 18.8580320137437 | 0
2023-10-19T10:01:00Z | -33.87898648664232 | 18.9167671810873 | 1154.620149696233
2023-10-19T10:02:00Z | -33.9236372451078 | 18.90859236742706 | 314.8444056522658
2023-10-19T10:03:00Z | -33.93977322434046 | 18.86983731460449 | 121.9898685716597
2023-10-19T10:04:00Z | -33.94716150047162 | 18.83893303296002 | 84.42383828343549
2023-10-19T10:05:00Z | -33.92095690015613 | 18.84204025975165 | 135.0077851301697

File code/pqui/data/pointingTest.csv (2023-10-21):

datetime | latitude | longitude | altitude
2023-10-20T13:18:00Z | -33.86722044711264 | 18.8580320137437 | 0
2023-10-20T13:18:20Z | -33.86722044711264 | 18.8580320137437 | 0
2023-10-20T13:18:20Z | -33.87898648664232 | 18.9167671810873 | 1000.0
2023-10-20T13:18:40Z | -33.87898648664232 | 18.9167671810873 | 1000.0
2023-10-20T13:18:40Z | -33.9236372451078 | 18.90859236742706 | 2000.0
2023-10-20T13:19:00Z | -33.9236372451078 | 18.90859236742706 | 2000.0
2023-10-20T13:19:00Z | -33.93977322434046 | 18.86983731460449 | 3000.0
2023-10-20T13:19:20Z | -33.93977322434046 | 18.86983731460449 | 3000.0
2023-10-20T13:19:20Z | -33.94716150047162 | 18.83893303296002 | 4000.0
2023-10-20T13:19:40Z | -33.94716150047162 | 18.83893303296002 | 4000.0
2023-10-20T13:19:40Z | -33.92095690015613 | 18.84204025975165 | 5000.0

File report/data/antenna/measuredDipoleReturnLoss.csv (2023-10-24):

Freq(Hz) | S11(DB) | S11(DEG)
100000000 | -0.42449361 | -64.158607
100600000 | -0.42548442 | -64.515503
101200000 | -0.42708129 | -64.88224
101800000 | -0.43108067 | -65.263268
102400000 | -0.43232736 | -65.628944
103000000 | -0.43416929 | -66.034462
103600000 | -0.43851969 | -66.413803
104200000 | -0.43945915 | -66.803833
104800000 | -0.44330791 | -67.182365
105400000 | -0.4444952 | -67.586601
106000000 | -0.44946754 | -67.982475
106600000 | -0.45792556 | -68.385696
107200000 | -0.46008316 | -68.778
107800000 | -0.4680877 | -69.184875
108400000 | -0.47115171 | -69.517342
109000000 | -0.48110282 | -69.924637
109600000 | -0.49045217 | -70.248306
110200000 | -0.49239725 | -70.611465
110800000 | -0.50075418 | -70.902863
111400000 | -0.49063438 | -71.289558
112000000 | -0.48489359 | -71.619339
112600000 | -0.48881793 | -72.007759
113200000 | -0.48095658 | -72.392792
113800000 | -0.47891235 | -72.78138
114400000 | -0.48029345 | -73.196838
115000000 | -0.47755823 | -73.584404
115600000 | -0.48223546 | -74.031807
116200000 | -0.48383492 | -74.431129
116800000 | -0.48520854 | -74.832428
117400000 | -0.49664557 | -75.249352
118000000 | -0.49401987 | -75.653687
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

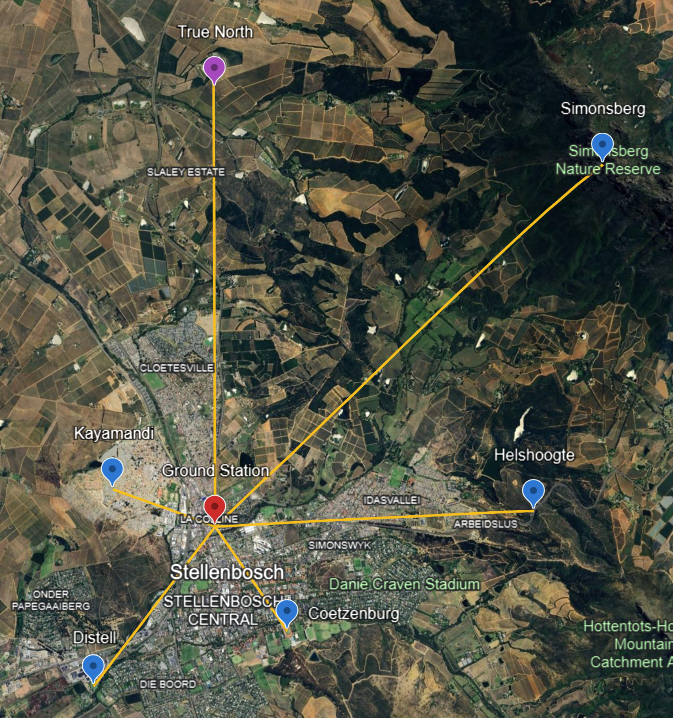
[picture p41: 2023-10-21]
report/endmatter/figures/pointingTestMap.png

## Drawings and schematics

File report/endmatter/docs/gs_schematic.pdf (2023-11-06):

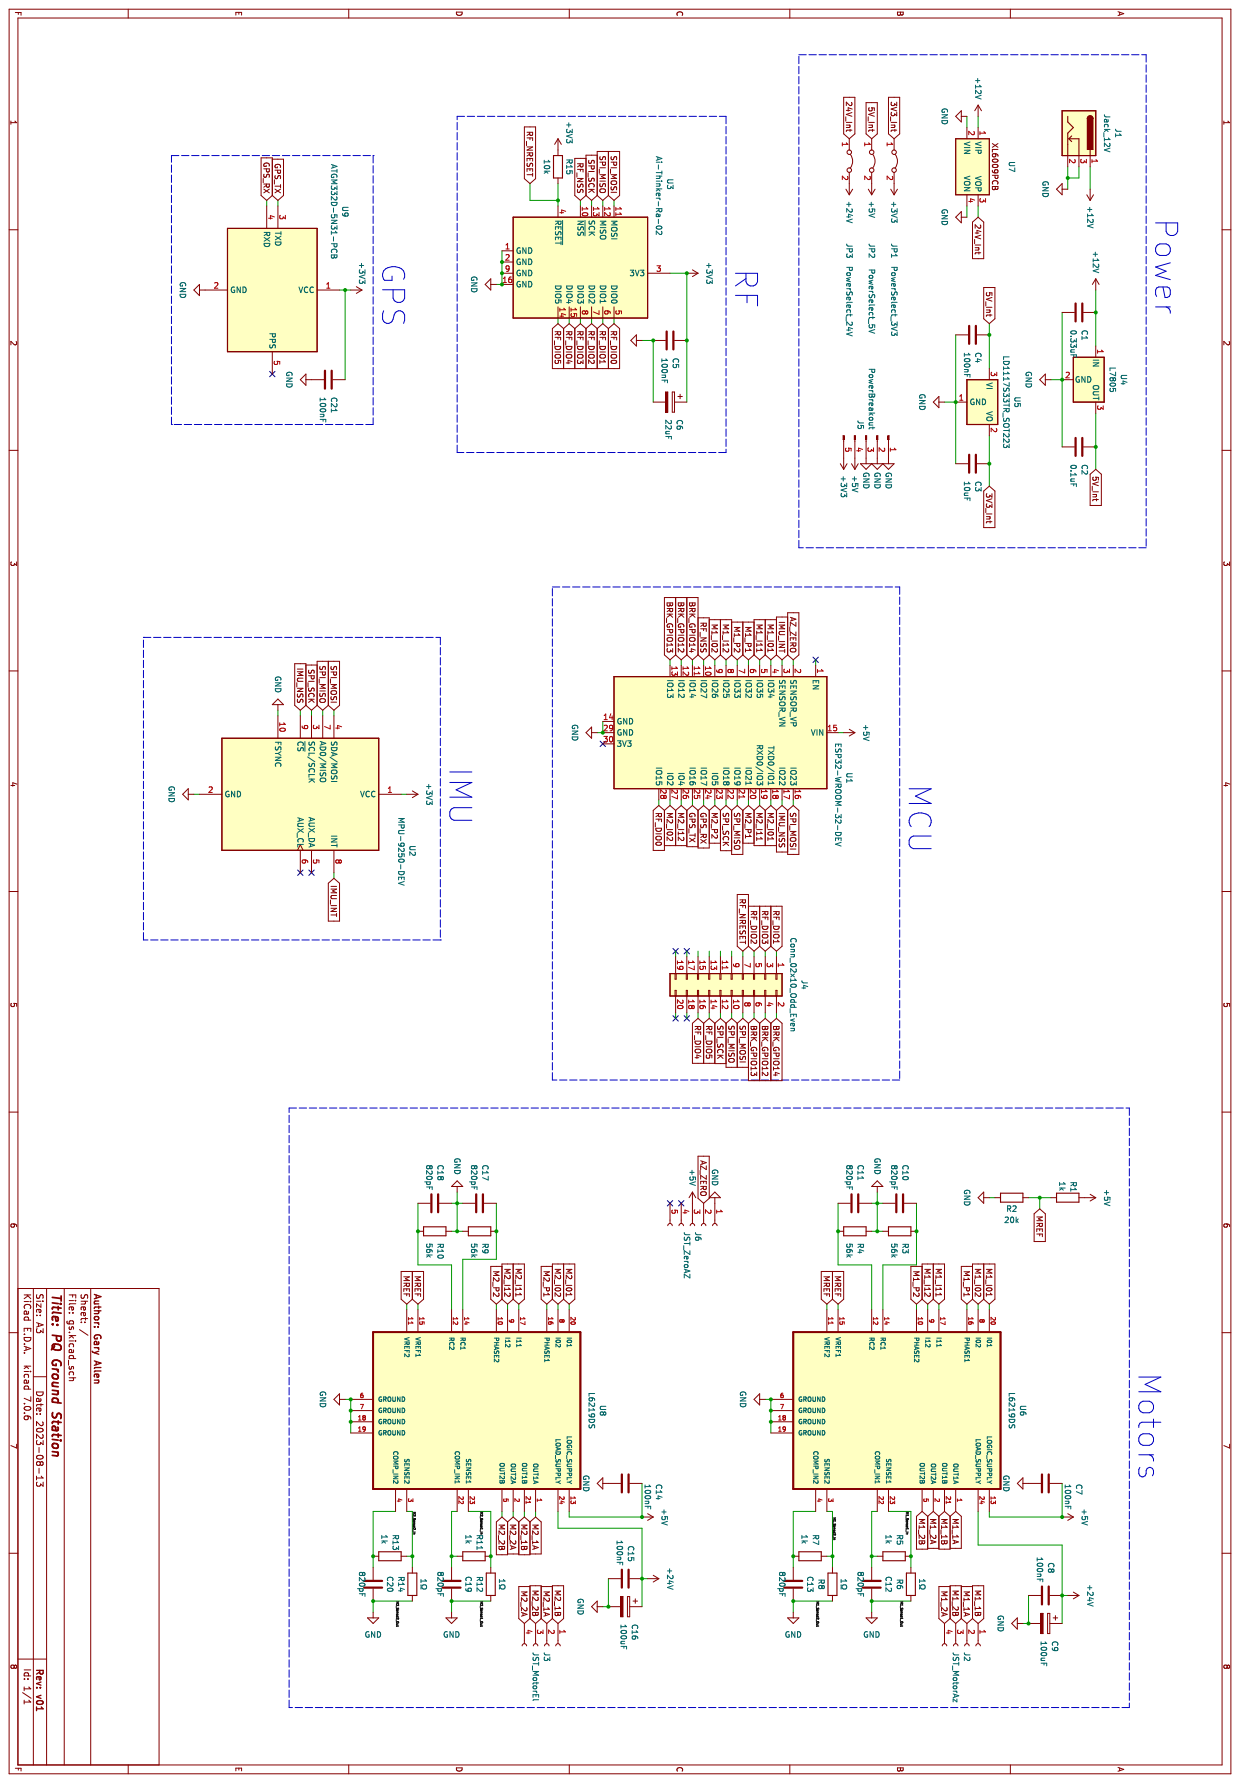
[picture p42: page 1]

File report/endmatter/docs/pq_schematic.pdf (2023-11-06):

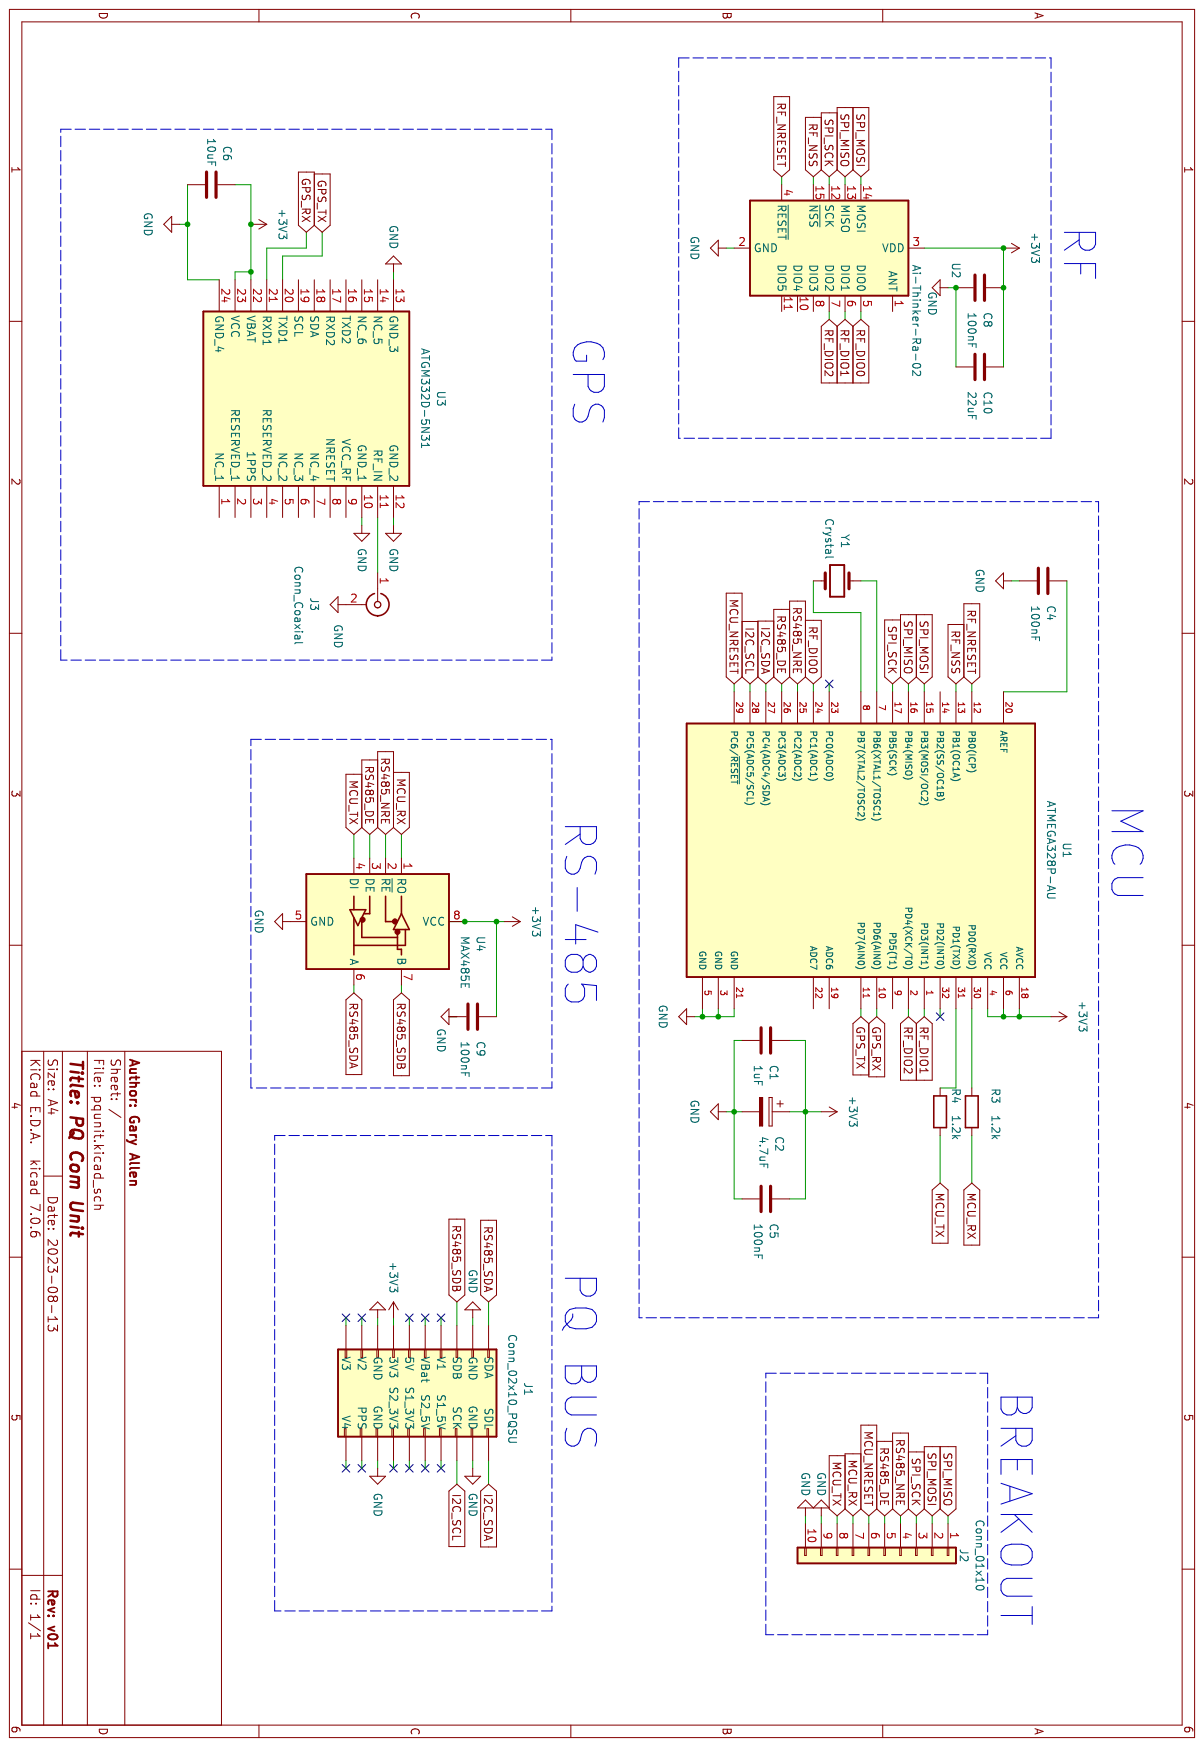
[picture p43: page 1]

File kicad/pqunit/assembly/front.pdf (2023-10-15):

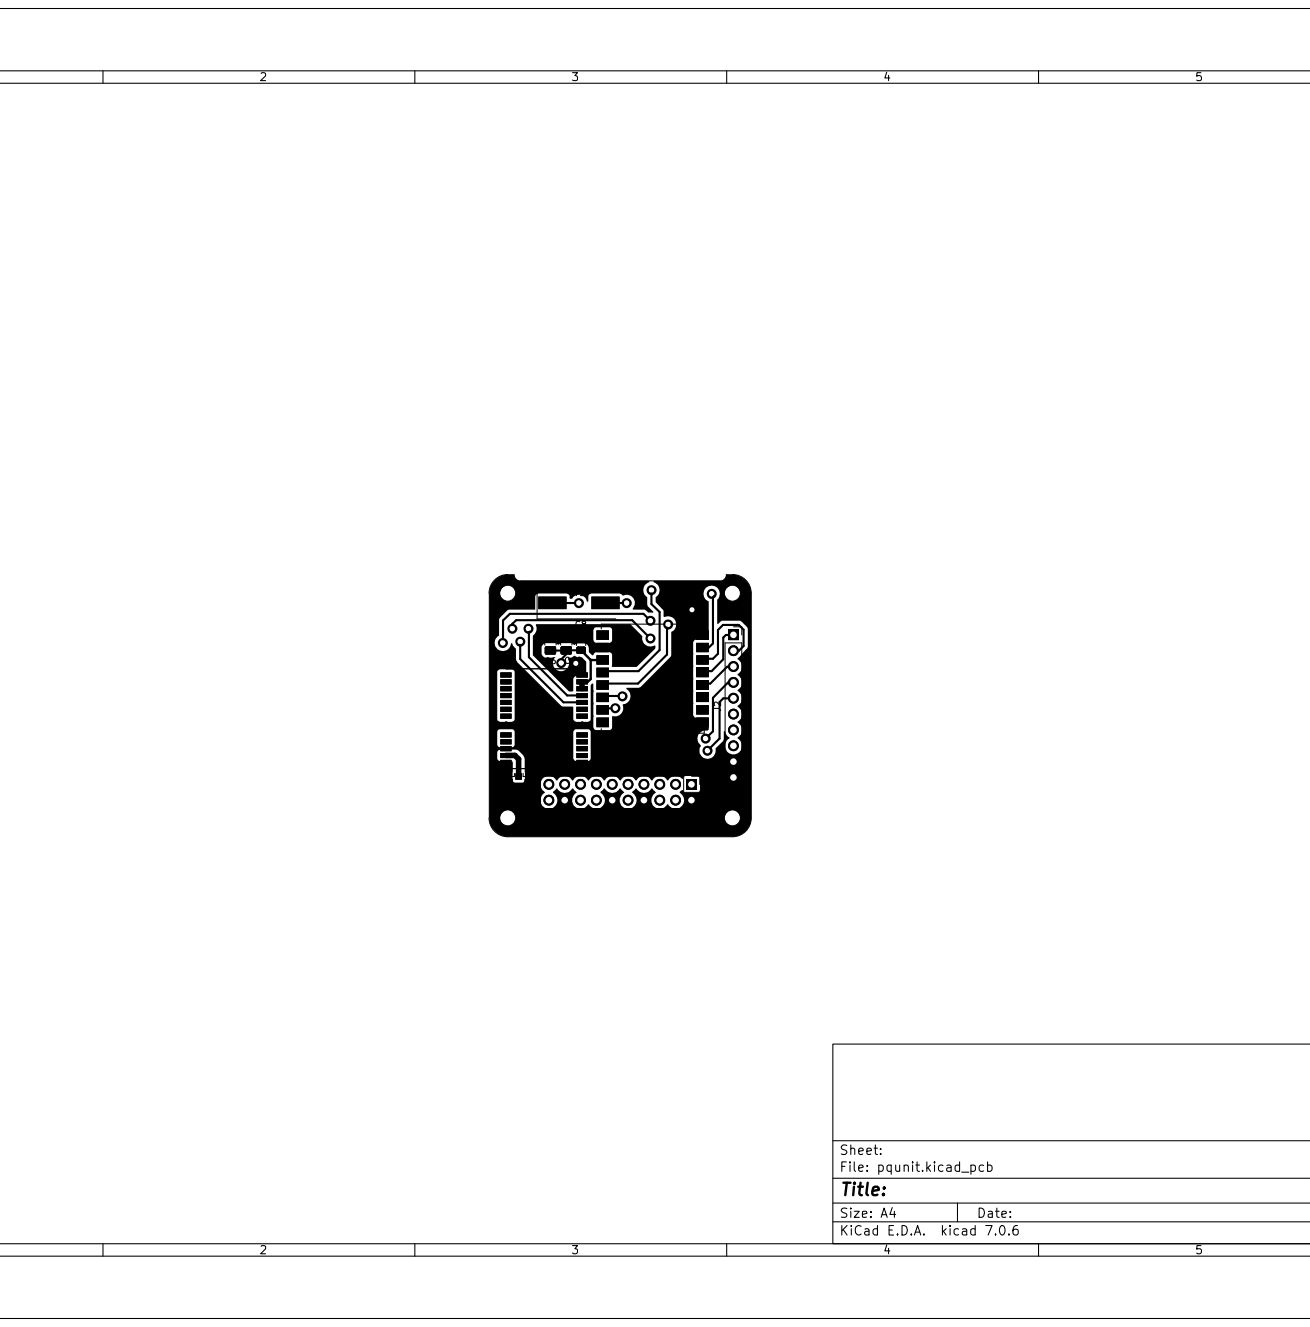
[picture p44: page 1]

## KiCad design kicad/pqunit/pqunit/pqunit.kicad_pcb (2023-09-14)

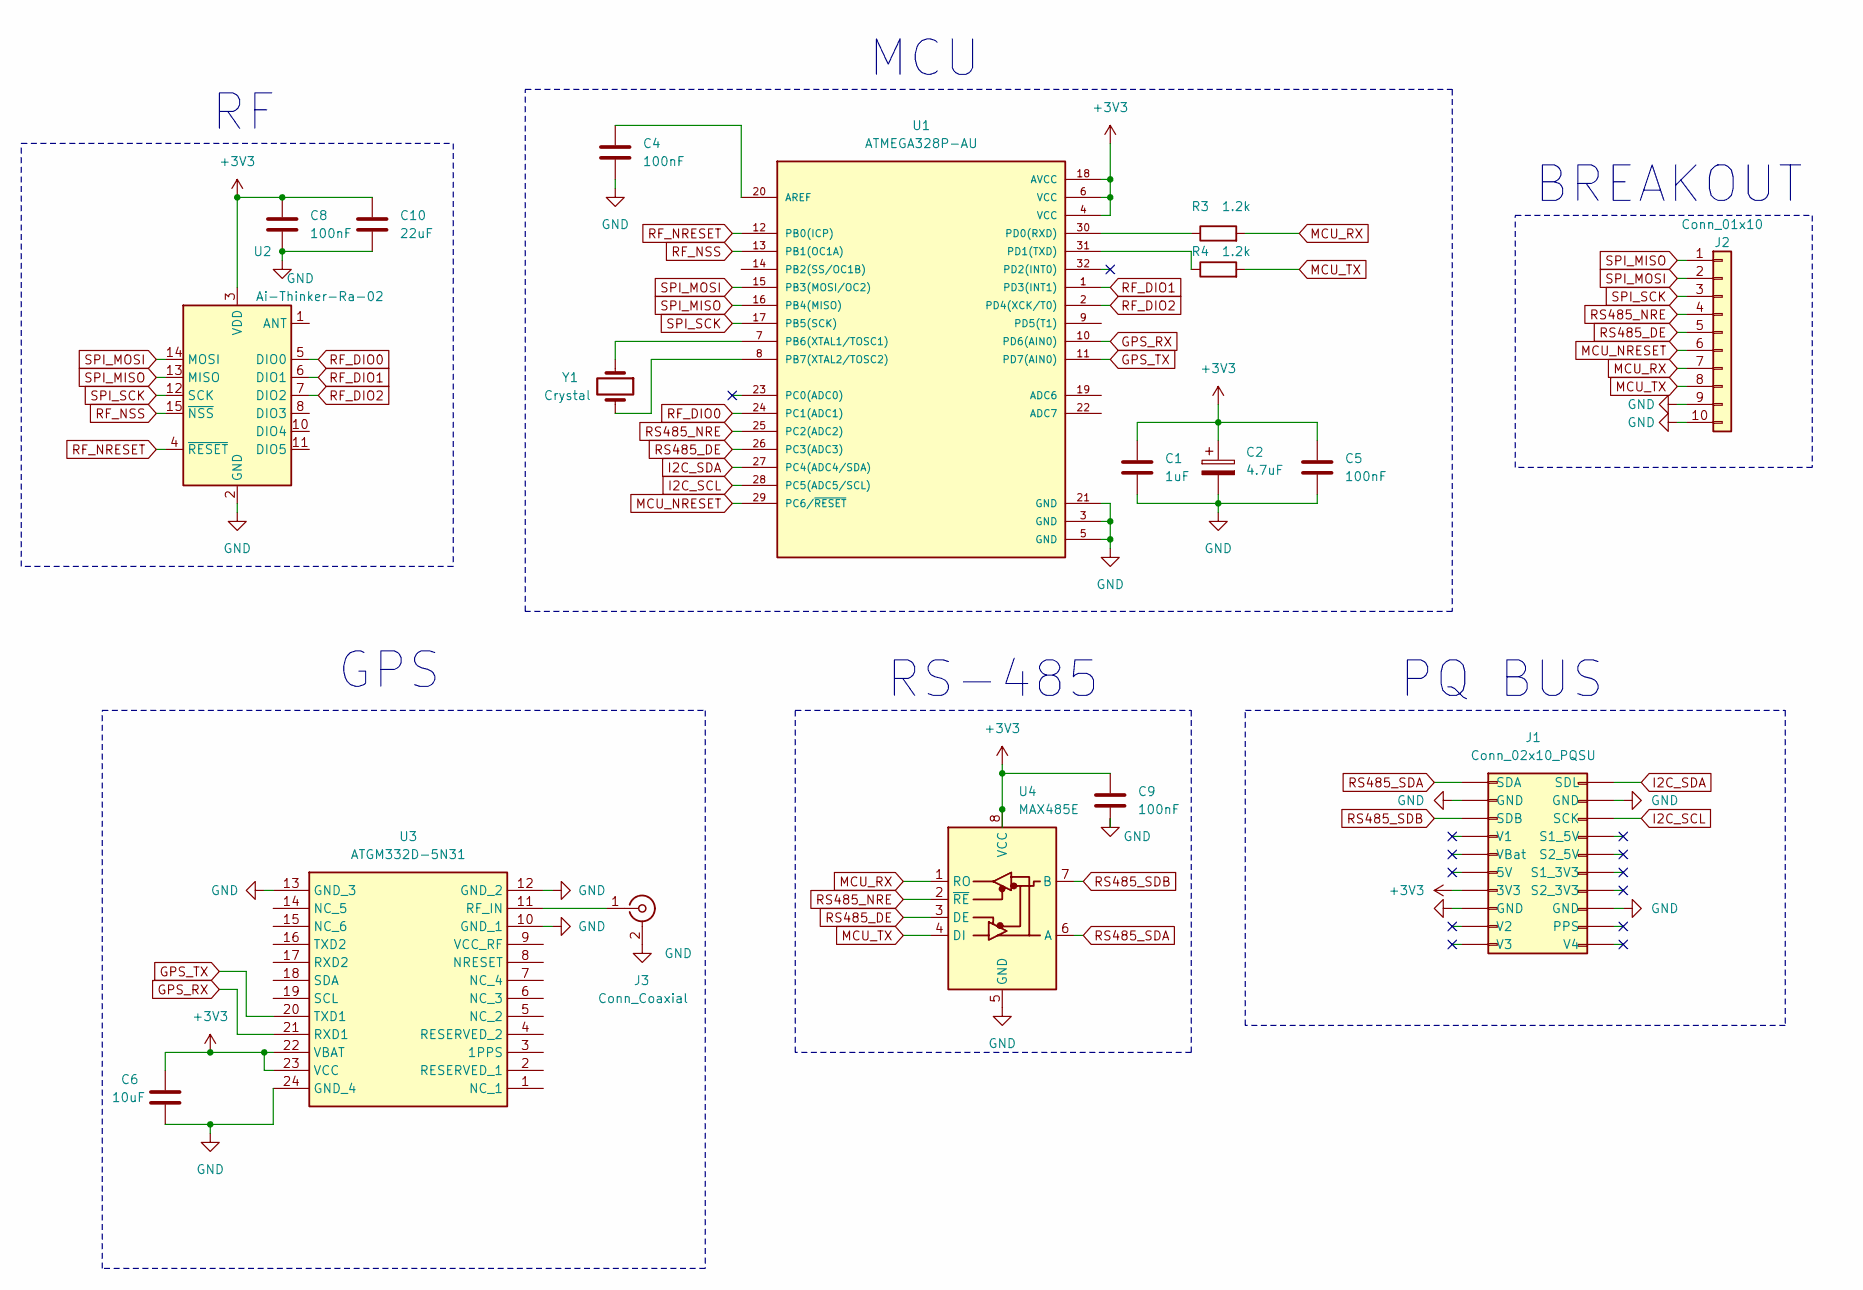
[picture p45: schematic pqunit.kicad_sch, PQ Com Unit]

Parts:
C1: 1uF; C_1206_3216Metric_Pad1.33x1.80mm_HandSolder
C2: 4.7uF; C_1206_3216Metric_Pad1.33x1.80mm_HandSolder
C4, C5, C8, C9: 100nF; C_0805_2012Metric_Pad1.18x1.45mm_HandSolder
C6: 10uF; C_1206_3216Metric_Pad1.33x1.80mm_HandSolder
C10: 22uF; C_1206_3216Metric_Pad1.33x1.80mm_HandSolder
J1: Conn_02x10_PQSU; PinSocket_2x10_P2.54mm_Vertical
J2: Conn_01x10; PinSocket_1x10_P2.54mm_Vertical
J3: Conn_Coaxial; U.FL_Molex_MCRF_73412-0110_Vertical
R3, R4: 1.2k; R_0805_2012Metric_Pad1.20x1.40mm_HandSolder
U1: ATMEGA328P-AU; TQFP-32_7x7mm_P0.8mm
U2: Ai-Thinker-Ra-02; Ai-Thinker-Ra-01-LoRa
U3: ATGM332D-5N31; ATGM332D5N31; Manufacturer_Part_Number ATGM332D-5N31
U4: MAX485E; SO08
Y1: Crystal; Crystal_SMD_HC49-SD

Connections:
+3V3: C1.1, C2.1, C5.1, C6.1, C8.1, C9.1, C10.1, J1.7 (3V3), U1.4 (VCC), U1.6 (VCC), U1.18 (AVCC), U2.3 (VDD), U3.22 (VBAT), U3.23 (VCC), U4.8 (VCC)
GND: C1.2, C2.2, C4.2, C5.2, C6.2, C8.2, C9.2, C10.2, J1.2 (GND), J1.8 (GND), J1.12 (GND), J1.18 (GND), J2.9, J2.10, J3.2 (Ext), U1.3 (GND), U1.5 (GND), U1.21 (GND), U2.2 (GND), U2.9 (GND), U2.16 (GND), U3.10 (GND_1), U3.12 (GND_2), U3.13 (GND_3), U3.24 (GND_4), U4.5 (GND)
GPS_RX: U1.10 (PD6(AIN0)), U3.21 (RXD1)
GPS_TX: U1.11 (PD7(AIN0)), U3.20 (TXD1)
I2C_SCL: J1.13 (SCK), U1.28 (PC5(ADC5/SCL))
I2C_SDA: J1.11 (SDL), U1.27 (PC4(ADC4/SDA))
MCU_NRESET: J2.6, U1.29 (PC6/~RESET)
MCU_RX: J2.7, R3.2, U4.1 (RO)
MCU_TX: J2.8, R4.2, U4.4 (DI)
unnamed: J3.1 (In), U3.11 (RF_IN)
unnamed: C4.1, U1.20 (AREF)
unnamed: U1.7 (PB6(XTAL1/TOSC1)), Y1.1
unnamed: U1.8 (PB7(XTAL2/TOSC2)), Y1.2
unnamed: R3.1, U1.30 (PD0(RXD))
unnamed: R4.1, U1.31 (PD1(TXD))
RF_DIO0: U1.24 (PC1(ADC1)), U2.5 (DIO0)
RF_DIO1: U1.1 (PD3(INT1)), U2.6 (DIO1)
RF_DIO2: U1.2 (PD4(XCK/T0)), U2.7 (DIO2)
RF_NRESET: U1.12 (PB0(ICP)), U2.4 (~RESET)
RF_NSS: U1.13 (PB1(OC1A)), U2.15 (~NSS)
RS485_DE: J2.5, U1.26 (PC3(ADC3)), U4.3 (DE)
RS485_NRE: J2.4, U1.25 (PC2(ADC2)), U4.2 (~RE)
RS485_SDA: J1.1 (SDA), U4.6 (A)
RS485_SDB: J1.3 (SDB), U4.7 (B)
SPI_MISO: J2.1, U1.16 (PB4(MISO)), U2.13 (MISO)
SPI_MOSI: J2.2, U1.15 (PB3(MOSI/OC2)), U2.14 (MOSI)
SPI_SCK: J2.3, U1.17 (PB5(SCK)), U2.12 (SCK)

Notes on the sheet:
PQ BUS
GPS
MCU
BREAKOUT
RS-485

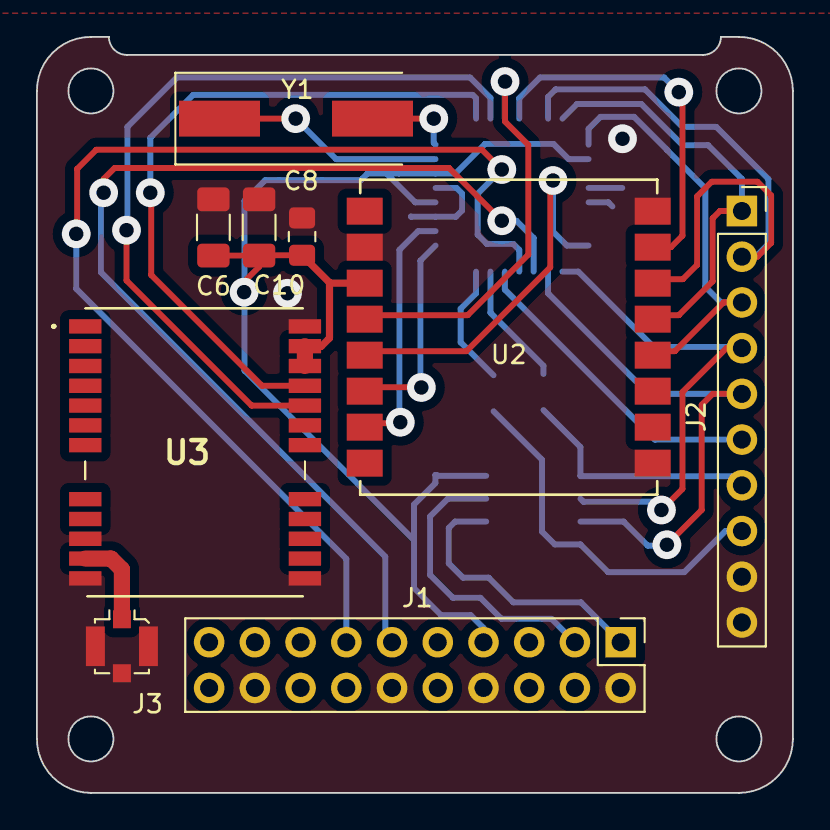
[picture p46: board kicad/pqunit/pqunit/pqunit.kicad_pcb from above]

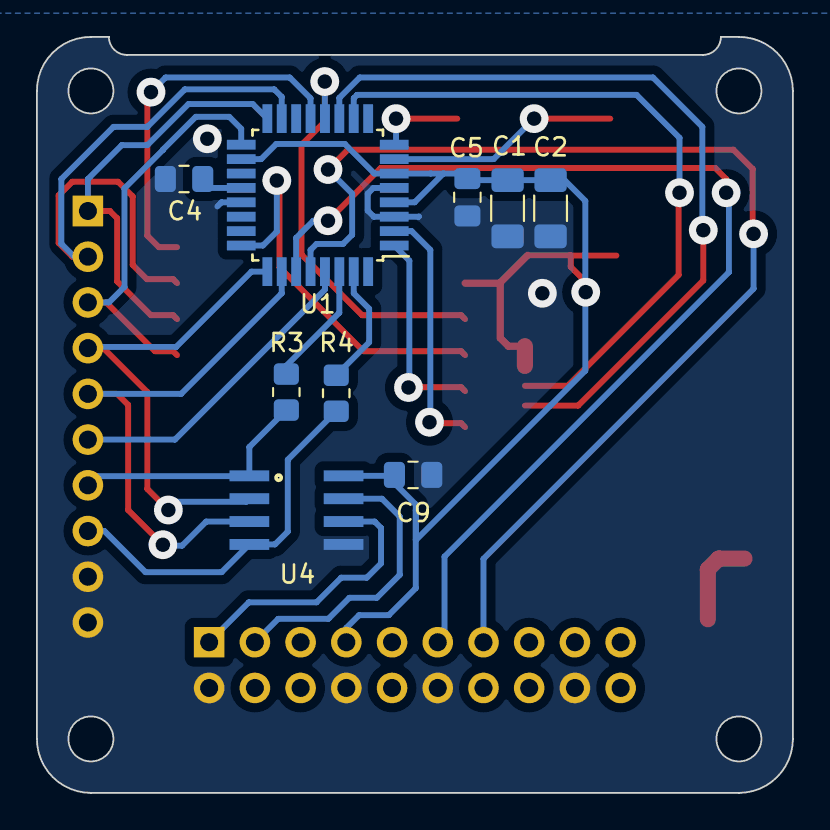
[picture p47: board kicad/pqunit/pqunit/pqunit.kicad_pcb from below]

Board: 2 copper layers, 42.0 x 42.0 mm, 18 parts (9 on the bottom side), 27 nets.

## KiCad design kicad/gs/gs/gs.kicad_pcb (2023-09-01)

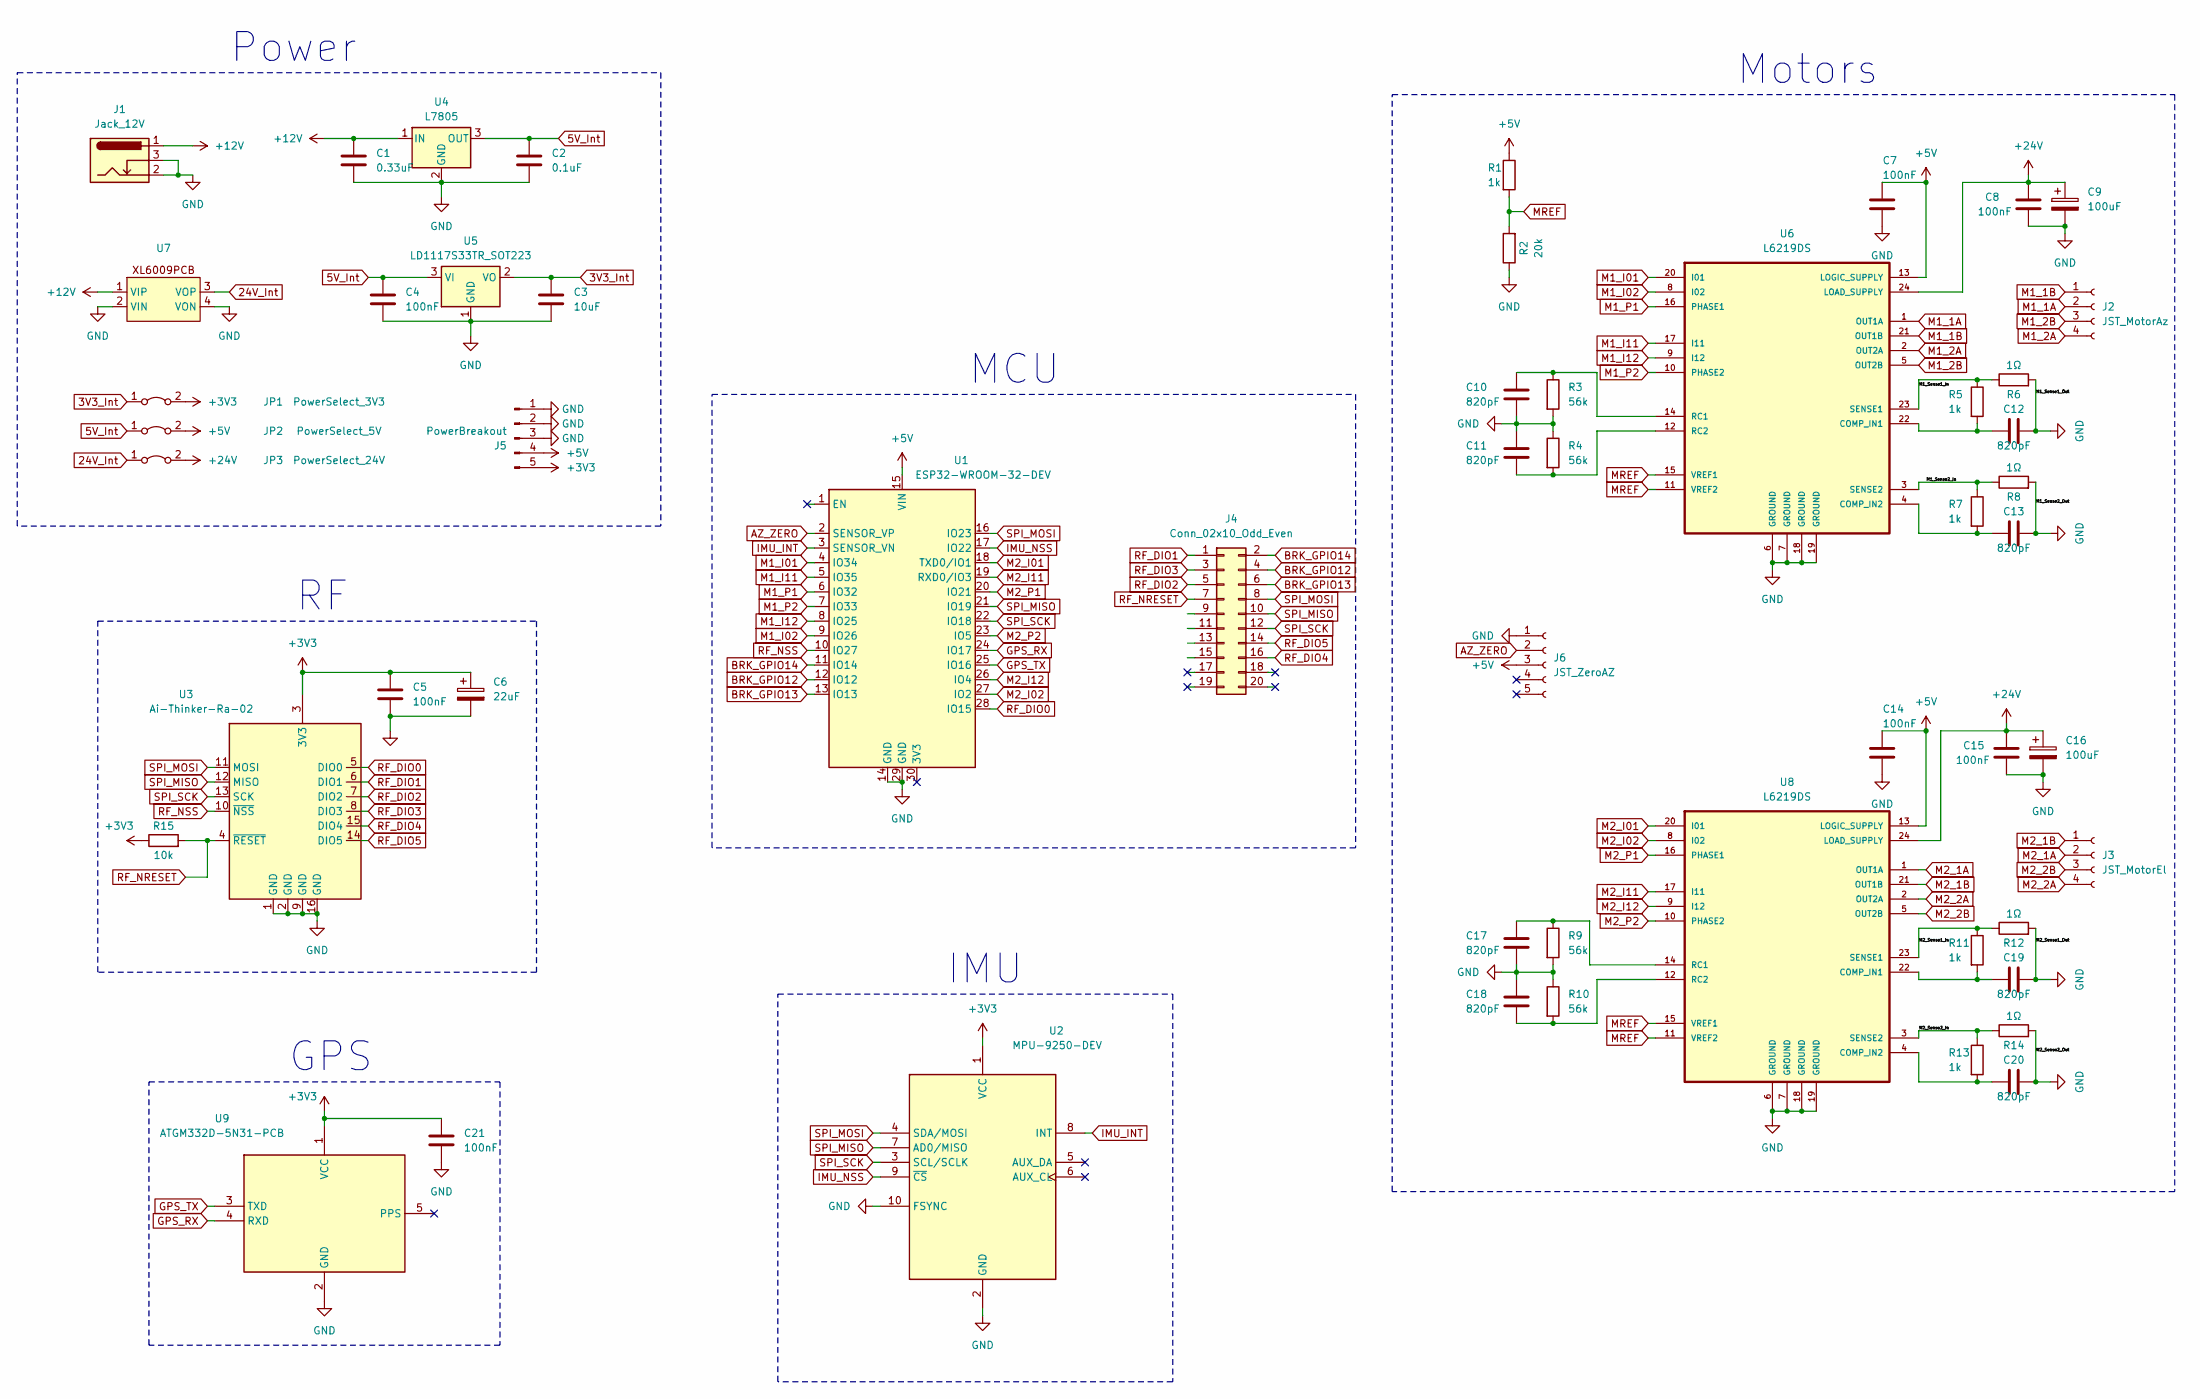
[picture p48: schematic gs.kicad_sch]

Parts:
C1: 0.33uF; C_Rect_L7.0mm_W4.5mm_P5.00mm
C2: 0.1uF; C_Rect_L7.0mm_W4.5mm_P5.00mm
C3: 10uF; C_Rect_L7.0mm_W4.5mm_P5.00mm
C4, C5, C7, C8, C14, C15, C21: 100nF; C_Rect_L7.0mm_W4.5mm_P5.00mm
C6: 22uF; CP_Radial_D5.0mm_P2.00mm
C9, C16: 100uF; CP_Radial_D5.0mm_P2.00mm
C10, C11, C12, C13, C17, C18, C19, C20: 820pF; C_Rect_L4.6mm_W2.0mm_P2.50mm_MKS02_FKP02
J1: Jack_12V; BarrelJack_Kycon_KLDX-0202-xC_Horizontal
J2: JST_MotorAz; JST_PH_B4B-PH-K_1x04_P2.00mm_Vertical
J3: JST_MotorEl; JST_PH_B4B-PH-K_1x04_P2.00mm_Vertical
J4: Conn_02x10_Odd_Even; PinHeader_2x10_P2.54mm_Vertical
J5: PowerBreakout; PinHeader_1x05_P2.54mm_Vertical
J6: JST_ZeroAZ; JST_PH_B5B-PH-K_1x05_P2.00mm_Vertical
JP1: PowerSelect_3V3; PinHeader_1x02_P2.54mm_Vertical
JP2: PowerSelect_5V; PinHeader_1x02_P2.54mm_Vertical
JP3: PowerSelect_24V; PinHeader_1x02_P2.54mm_Vertical
R1, R5, R7, R11, R13: 1k; R_Axial_DIN0207_L6.3mm_D2.5mm_P10.16mm_Horizontal
R2: 20k; R_Axial_DIN0207_L6.3mm_D2.5mm_P10.16mm_Horizontal
R3, R4, R9, R10: 56k; R_Axial_DIN0207_L6.3mm_D2.5mm_P10.16mm_Horizontal
R6, R8, R12, R14: 1Ω; R_Axial_DIN0207_L6.3mm_D2.5mm_P10.16mm_Horizontal
R15: 10k; R_Axial_DIN0207_L6.3mm_D2.5mm_P10.16mm_Horizontal
U1: ESP32-WROOM-32-DEV; ESP32-WROOM-32PCB
U2: MPU-9250-DEV; MPU-9250-PCB
U3: Ai-Thinker-Ra-02; RA-02-PCB
U4: L7805; TO-220-3_Horizontal_TabDown
U5: LD1117S33TR_SOT223; TO-220-3_Horizontal_TabDown
U6, U8: L6219DS; SOIC127P1030X265-24N
U7: XL6009PCB
U9: ATGM332D-5N31-PCB; Manufacturer_Part_Number ATGM332D-5N31

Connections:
3V3_Int: C3.1, JP1.1 (A), U5.2 (VO)
5V_Int: C2.1, C4.1, JP2.1 (A), U4.3 (OUT), U5.3 (VI)
24V_Int: JP3.1 (A), U7.3 (VOP)
+3V3: C5.1, C6.1, C21.1, J5.5, JP1.2 (B), R15.1, U2.1 (VCC), U3.3 (3V3), U9.1 (VCC)
+5V: C7.1, C14.1, J5.4, J6.3, JP2.2 (B), R1.1, U1.15 (VIN), U6.13 (LOGIC_SUPPLY), U8.13 (LOGIC_SUPPLY)
+12V: C1.1, J1.1, U4.1 (IN), U7.1 (VIP)
+24V: C8.1, C9.1, C15.1, C16.1, JP3.2 (B), U6.24 (LOAD_SUPPLY), U8.24 (LOAD_SUPPLY)
/M1_Sense1_In: R5.1, R6.1, U6.23 (SENSE1)
/M1_Sense2_In: R7.1, R8.1, U6.3 (SENSE2)
/M2_Sense1_In: R11.1, R12.1, U8.23 (SENSE1)
/M2_Sense2_In: R13.1, R14.1, U8.3 (SENSE2)
AZ_ZERO: J6.2, U1.2 (SENSOR_VP)
BRK_GPIO12: J4.4, U1.12 (IO12)
BRK_GPIO13: J4.6, U1.13 (IO13)
BRK_GPIO14: J4.2, U1.11 (IO14)
GND: C1.2, C2.2, C3.2, C4.2, C5.2, C6.2, C7.2, C8.2, C9.2, C10.2, C11.1, C12.1, C13.1, C14.2, C15.2, C16.2, C17.2, C18.1, C19.1, C20.1, C21.2, J1.2, J1.3, J5.1, J5.2, J5.3, J6.1, R2.1, R3.2, R4.1, R6.2, R8.2, R9.2, R10.1, R12.2, R14.2, U1.14 (GND), U1.29 (GND), U2.2 (GND), U2.10 (FSYNC), U3.1 (GND), U3.2 (GND), U3.9 (GND), U3.16 (GND), U4.2 (GND), U5.1 (GND), U6.6 (GROUND), U6.7 (GROUND), U6.18 (GROUND), U6.19 (GROUND), U7.2 (VIN), U7.4 (VON), U8.6 (GROUND), U8.7 (GROUND), U8.18 (GROUND), U8.19 (GROUND), U9.2 (GND)
GPS_RX: U1.24 (IO17), U9.4 (RXD)
GPS_TX: U1.25 (IO16), U9.3 (TXD)
IMU_INT: U1.3 (SENSOR_VN), U2.8 (INT)
IMU_NSS: U1.17 (IO22), U2.9 (~CS)
M1_1A: J2.2, U6.1 (OUT1A)
M1_1B: J2.1, U6.21 (OUT1B)
M1_2A: J2.4, U6.2 (OUT2A)
M1_2B: J2.3, U6.5 (OUT2B)
M1_I01: U1.4 (IO34), U6.20 (I01)
M1_I02: U1.9 (IO26), U6.8 (I02)
M1_I11: U1.5 (IO35), U6.17 (I11)
M1_I12: U1.8 (IO25), U6.9 (I12)
M1_P1: U1.6 (IO32), U6.16 (PHASE1)
M1_P2: U1.7 (IO33), U6.10 (PHASE2)
M2_1A: J3.2, U8.1 (OUT1A)
M2_1B: J3.1, U8.21 (OUT1B)
M2_2A: J3.4, U8.2 (OUT2A)
M2_2B: J3.3, U8.5 (OUT2B)
M2_I01: U1.18 (TXD0/IO1), U8.20 (I01)
M2_I02: U1.27 (IO2), U8.8 (I02)
M2_I11: U1.19 (RXD0/IO3), U8.17 (I11)
M2_I12: U1.26 (IO4), U8.9 (I12)
M2_P1: U1.20 (IO21), U8.16 (PHASE1)
M2_P2: U1.23 (IO5), U8.10 (PHASE2)
MREF: R1.2, R2.2, U6.11 (VREF2), U6.15 (VREF1), U8.11 (VREF2), U8.15 (VREF1)
unnamed: C12.2, R5.2, U6.22 (COMP_IN1)
unnamed: C13.2, R7.2, U6.4 (COMP_IN2)
unnamed: C10.1, R3.1, U6.14 (RC1)
unnamed: C11.2, R4.2, U6.12 (RC2)
unnamed: C19.2, R11.2, U8.22 (COMP_IN1)
unnamed: C20.2, R13.2, U8.4 (COMP_IN2)
unnamed: C17.1, R9.1, U8.14 (RC1)
unnamed: C18.2, R10.2, U8.12 (RC2)
RF_DIO0: U1.28 (IO15), U3.5 (DIO0)
RF_DIO1: J4.1, U3.6 (DIO1)
RF_DIO2: J4.5, U3.7 (DIO2)
RF_DIO3: J4.3, U3.8 (DIO3)
RF_DIO4: J4.16, U3.15 (DIO4)
RF_DIO5: J4.14, U3.14 (DIO5)
RF_NRESET: J4.7, R15.2, U3.4 (~RESET)
RF_NSS: U1.10 (IO27), U3.10 (~NSS)
SPI_MISO: J4.10, U1.21 (IO19), U2.7 (AD0/MISO), U3.12 (MISO)
SPI_MOSI: J4.8, U1.16 (IO23), U2.4 (SDA/MOSI), U3.11 (MOSI)
SPI_SCK: J4.12, U1.22 (IO18), U2.3 (SCL/SCLK), U3.13 (SCK)

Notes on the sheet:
Power
MCU
Motors
IMU
GPS

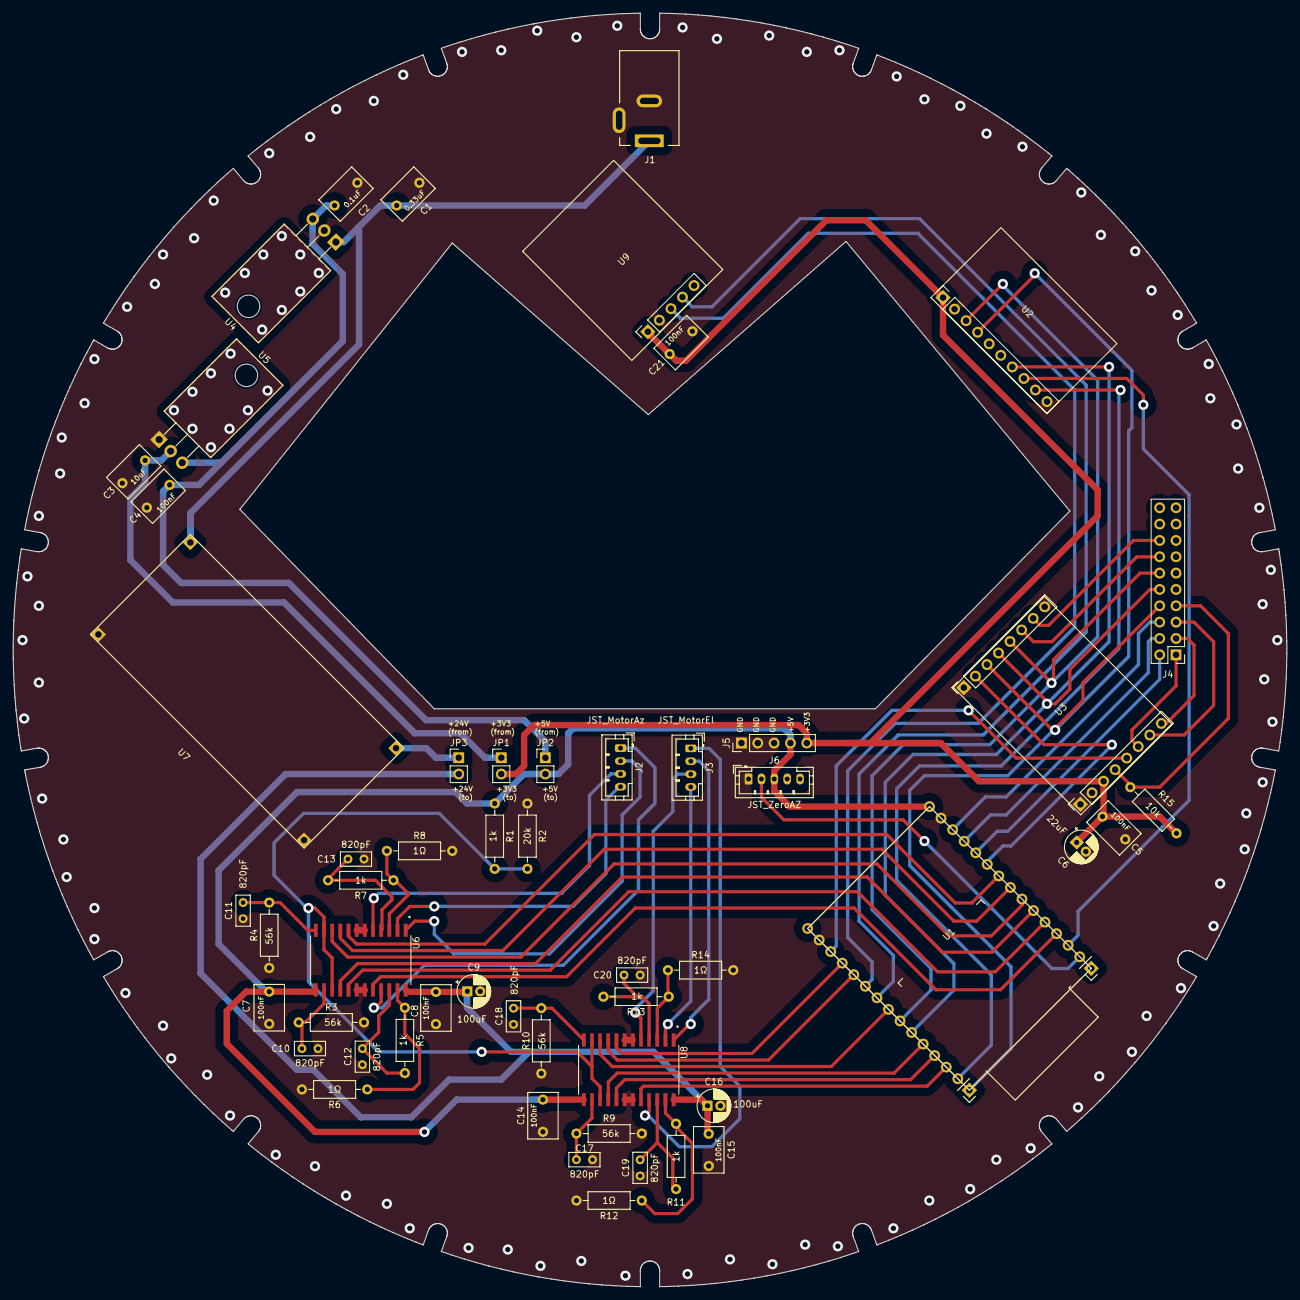
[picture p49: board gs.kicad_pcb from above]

Board: 2 copper layers, 198.0 x 198.0 mm, 54 parts (0 on the bottom side), 60 nets.

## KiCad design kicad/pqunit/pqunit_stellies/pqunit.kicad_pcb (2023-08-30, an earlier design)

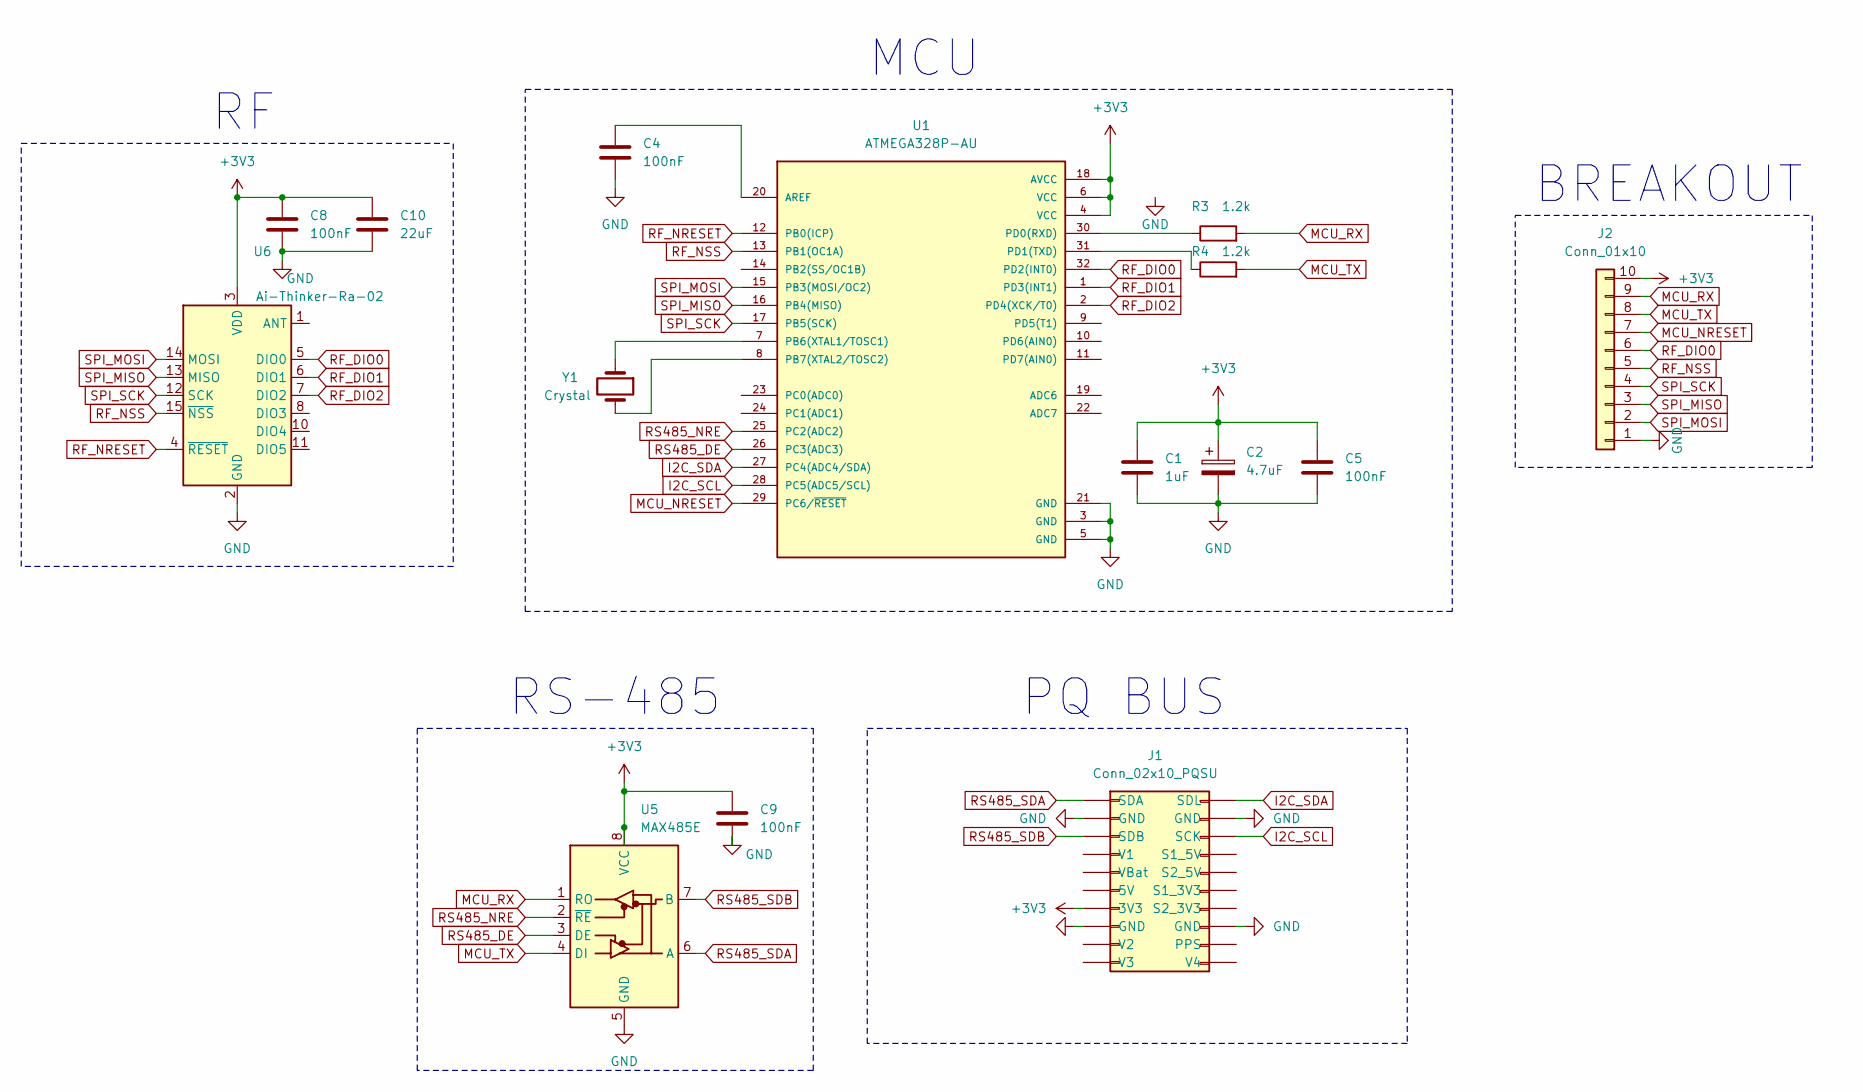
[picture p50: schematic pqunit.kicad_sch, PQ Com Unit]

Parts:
C1: 1uF; C_0805_2012Metric_Pad1.18x1.45mm_HandSolder
C2: 4.7uF; C_1206_3216Metric_Pad1.33x1.80mm_HandSolder
C4, C5, C8, C9: 100nF; C_0603_1608Metric_Pad1.08x0.95mm_HandSolder
C10: 22uF; C_0805_2012Metric_Pad1.18x1.45mm_HandSolder
J1: Conn_02x10_PQSU; PinSocket_2x10_P2.54mm_Vertical
J2: Conn_01x10; PinSocket_1x10_P2.54mm_Vertical
R3, R4: 1.2k; R_0805_2012Metric_Pad1.20x1.40mm_HandSolder
U1: ATMEGA328P-AU; TQFP-32_7x7mm_P0.8mm
U5: MAX485E; SO08
U6: Ai-Thinker-Ra-02; Ai-Thinker-Ra-01-LoRa
Y1: Crystal; Crystal_SMD_HC49-SD

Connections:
+3V3: C1.1, C2.1, C5.1, C8.1, C9.1, C10.1, J1.7 (3V3), J2.10, U1.4 (VCC), U1.6 (VCC), U1.18 (AVCC), U5.8 (VCC), U6.3 (VDD)
GND: C1.2, C2.2, C4.2, C5.2, C8.2, C9.2, C10.2, J1.2 (GND), J1.8 (GND), J1.12 (GND), J1.18 (GND), J2.1, U1.3 (GND), U1.5 (GND), U1.21 (GND), U5.5 (GND), U6.2 (GND), U6.9 (GND), U6.16 (GND)
I2C_SCL: J1.13 (SCK), U1.28 (PC5(ADC5/SCL))
I2C_SDA: J1.11 (SDL), U1.27 (PC4(ADC4/SDA))
MCU_NRESET: J2.7, U1.29 (PC6/~RESET)
MCU_RX: J2.9, R3.2, U5.1 (RO)
MCU_TX: J2.8, R4.2, U5.4 (DI)
unnamed: C4.1, U1.20 (AREF)
unnamed: U1.7 (PB6(XTAL1/TOSC1)), Y1.1
unnamed: U1.8 (PB7(XTAL2/TOSC2)), Y1.2
unnamed: R3.1, U1.30 (PD0(RXD))
unnamed: R4.1, U1.31 (PD1(TXD))
RF_DIO0: J2.6, U1.32 (PD2(INT0)), U6.5 (DIO0)
RF_DIO1: U1.1 (PD3(INT1)), U6.6 (DIO1)
RF_DIO2: U1.2 (PD4(XCK/T0)), U6.7 (DIO2)
RF_NRESET: U1.12 (PB0(ICP)), U6.4 (~RESET)
RF_NSS: J2.5, U1.13 (PB1(OC1A)), U6.15 (~NSS)
RS485_DE: U1.26 (PC3(ADC3)), U5.3 (DE)
RS485_NRE: U1.25 (PC2(ADC2)), U5.2 (~RE)
RS485_SDA: J1.1 (SDA), U5.6 (A)
RS485_SDB: J1.3 (SDB), U5.7 (B)
SPI_MISO: J2.3, U1.16 (PB4(MISO)), U6.13 (MISO)
SPI_MOSI: J2.2, U1.15 (PB3(MOSI/OC2)), U6.14 (MOSI)
SPI_SCK: J2.4, U1.17 (PB5(SCK)), U6.12 (SCK)

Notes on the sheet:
PQ BUS
MCU
BREAKOUT
RS-485

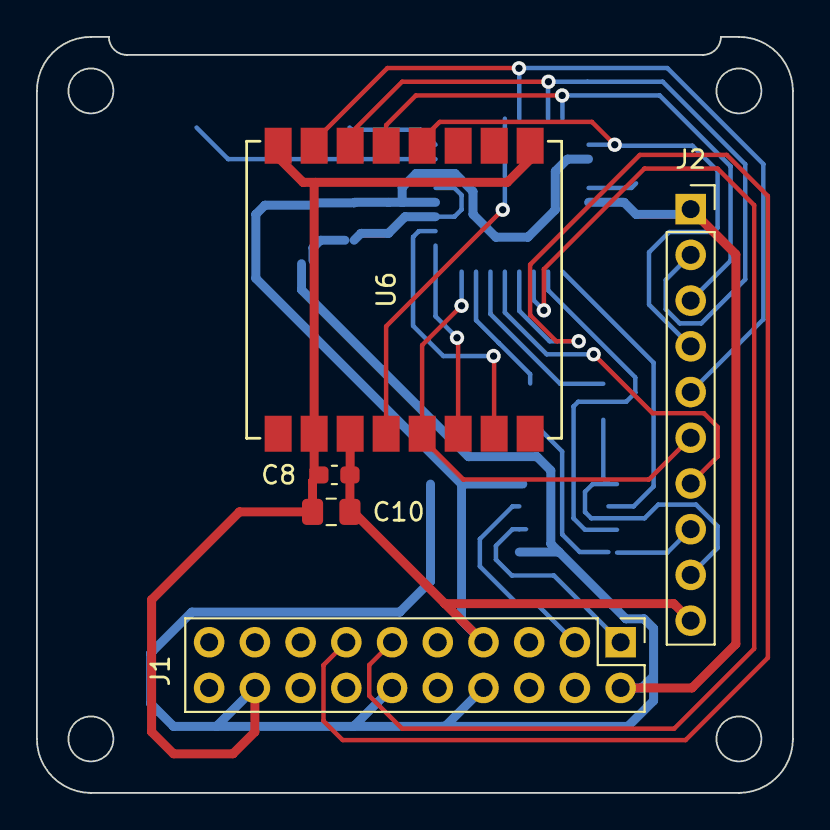
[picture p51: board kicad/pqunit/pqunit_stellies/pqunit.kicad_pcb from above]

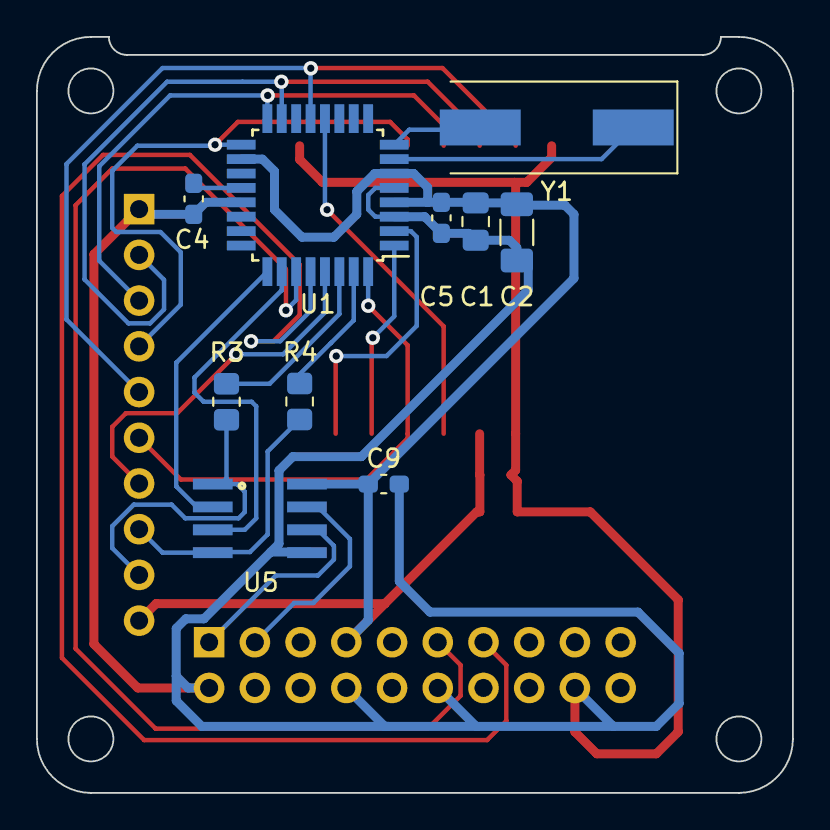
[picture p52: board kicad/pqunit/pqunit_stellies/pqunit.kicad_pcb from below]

Board: 2 copper layers, 42.0 x 42.0 mm, 15 parts (10 on the bottom side), 24 nets.

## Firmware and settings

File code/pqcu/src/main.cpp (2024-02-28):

#include "Settings.h"
#include "PqUnit.h"

#include <Arduino.h>
#include <gel.h>

PqUnit pq;

void setup()
{
    // Calibrated for Atmega328 on PQ unit developed in 2023 for 8 MHz internal clock.
    // If this line is not included, clock timing is not calibrated and software serial
    // with the GPS does not work.
    OSCCAL = 101;

    pq.begin();
}

void loop()
{
    pq.update(); 
}

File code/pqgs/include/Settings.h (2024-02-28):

// Serial comms
#define BAUD_RATE                               115200
#define FLIGHT_PATH_MAX_SIZE                    5120

// Mount control
#define MOUNT_EL_ANGLE_MIN                      (35.0)
#define MOUNT_EL_ANGLE_MAX                      140.0
#define MOUNT_AZEL_RATIO                        -1.15
#define MOUNT_EL_START_NEAR_CUTOUT              true
#define MOUNT_EL_NUM_STEPS                      (200.0 * (92.0/20.0) * (140.0/80.0))
#define MOUNT_AZ_NUM_STEPS                      (200.0 * (60.0/15.0))

// Ground station control
#define GS_ESTIMATED_BEAMWIDTH                  60.0
#define GS_NUM_BEAMWIDTH_SCAN_SEGMENTS          4
#define GS_NUM_AZIMUTH_SCAN_SAMPLES             20
#define GS_SCAN_TIMEOUT                         120
#define GS_KNOWN_LOCATION_TRUST_TIMEOUT         60
#define GS_UPDATE_INTERVAL                      100
#define GS_MNORTH_DELTA_AZ                      -74.0
#define GS_MAP_PROJECTION_ORIGIN_LAT            -34.0
#define GS_MAP_PROJECTION_ORIGIN_LONG           19.0
#define GS_DEFAULT_LOCATION_LAT                 -33.9321
#define GS_DEFAULT_LOCATION_LONG                18.8602

// Pins
#define PIN_AZ_ZERO_SENSOR              36
#define PIN_AZ_IO1                      14
#define PIN_AZ_IO2                      26
#define PIN_AZ_I11                      12
#define PIN_AZ_I12                      25
#define PIN_AZ_PH1                      32
#define PIN_AZ_PH2                      33
#define PIN_EL_IO1                      0
#define PIN_EL_IO2                      2
#define PIN_EL_I11                      16
#define PIN_EL_I12                      4
#define PIN_EL_PH1                      21
#define PIN_EL_PH2                      5
#define PIN_RADIO_NSS                   27
#define PIN_RADIO_DIO0                  15
#define PIN_RADIO_RESET                 13
#define PIN_IMU_NSS                     22
#define PIN_GPS_RX                      39
#define PIN_GPS_TX                      16

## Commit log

2023-08-12 Added documents
    [Gary Allen - Skripsie Components.xlsx, pqunit.kicad_pcb, pqunit.kicad_sch]
2023-08-12 Removed documents
    [Gary Allen - Skripsie Components.xlsx]
2023-08-20 Worked on schematics
    [ATMEGA328P-AU.step, XL6009.step, gs.kicad_pcb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]
2023-08-21 Finished first revision of PCBs
    [gs.kicad_pcb, gs.kicad_sch]
2023-08-30 Finished second revision of GS PCB
    [MAX485.step, gs.kicad_pcb, gs.kicad_sch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]
2023-09-01 2nd design of GS PCB
    [freerouting.dsn, gs.kicad_pcb, gs.kicad_sch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]
2023-09-01 Finished core of 2nd design of GS PCB
    [gs.kicad_pcb]
2023-09-01 Added details to GS PCB
    [gs.kicad_pcb]
2023-09-01 Finished GS PCB Rev 4
    [gs.kicad_pcb, gs.kicad_sch]
2023-09-01 Exported GS Rev 4 Gerbers
    [gs-B_Cu.gbr, gs-B_Mask.gbr, gs-B_Paste.gbr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]
2023-09-01 Fixed GS PCB Rev 4 problems to be Rev 4.1
    [gs-B_Cu.gbr, gs-B_Mask.gbr, gs-B_Paste.gbr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]
2023-09-01 Began PQUnit PCB Rev 2
    [pqunit.kicad_pcb, pqunit.kicad_sch]
2023-09-01 Fixed all PQUnit PCB Rev 2 errors
    [pqunit.kicad_pcb]
2023-09-03 Finished both PCB latest revisions
    [GS_PQ_BOM.xlsx, PQUnit_BOM.xlsx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]
2023-09-14 Updated PQ PCB to include GPS and added initial PIO code
    [CONUFL001-SMD.step, gs.kicad_pcb, gs.kicad_sch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]
2023-09-16 Added abstractions in code and created GEL repo
    [igrfgridData.csv]
2023-09-28 Started antenna design in report
2023-09-28 Added antenna design
2023-09-29 Finished antenna design
2023-09-29 Added helical antennap parameter table
2023-10-02 Reworked links to gel library
    [main.cpp]
2023-10-04 Calibrated mount elevation and added angle control
2023-10-04 Calibrated mount azimuthal and added compensation movement
2023-10-06 Finished mount spherical coord abstraction
2023-10-15 Added ISP
    [20231010-081400Z_-32.9716_18.1562_standard_profile_2023101000Z.csv, TableMountain.csv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]
2023-10-20 Ran further range tests and fixed PQ GPS
    [Settings.h, main.cpp]
2023-10-21 Performed 4.6km measurement
    [igrfgridData.csv]
2023-10-21 Performed GPS tracking test
    [HelicalUnoptimized.csv]
2023-10-22 Began reporting
    [dipoleReturnLoss.csv, helicalReturnLoss.csv]
2023-10-24 Finished first draft
    [combined_h.csv, combined_v.csv, dipoleReturnLoss.csv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]
2023-10-27 Added radiosonde reverse engineering
    [log_power_0.csv, station.cfg]
2023-10-28 Bug fixes
    [log_power_0.csv]
2023-11-01 Updated report
    [log_power_0.csv]
2023-11-02 Found motor bug
    [log_power_0.csv, station.cfg]
2023-11-04 Did 122km range test
    [1_fridayDay_prediction.csv, 1_fridayDay_track.csv, 20231010-081400Z_-32.9716_18.1562_standard_profile_2023101000Z.csv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]
2023-11-05 Worked on report
    [combined_h.csv, combined_v.csv, sundayDay_prediction.csv]
2023-11-06 Finished report
    [gs.kicad_sch, helicalImpedanceClose.csv, helicalImpedanceFar.csv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]
2024-02-28 Added final report
    [20231010-081400Z_-32.9716_18.1562_standard_profile_2023101000Z.csv, 2_fridayNight_prediction.csv, TableMountain.csv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]
